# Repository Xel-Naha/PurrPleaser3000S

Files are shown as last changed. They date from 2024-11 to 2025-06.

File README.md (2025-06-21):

<p align="center">
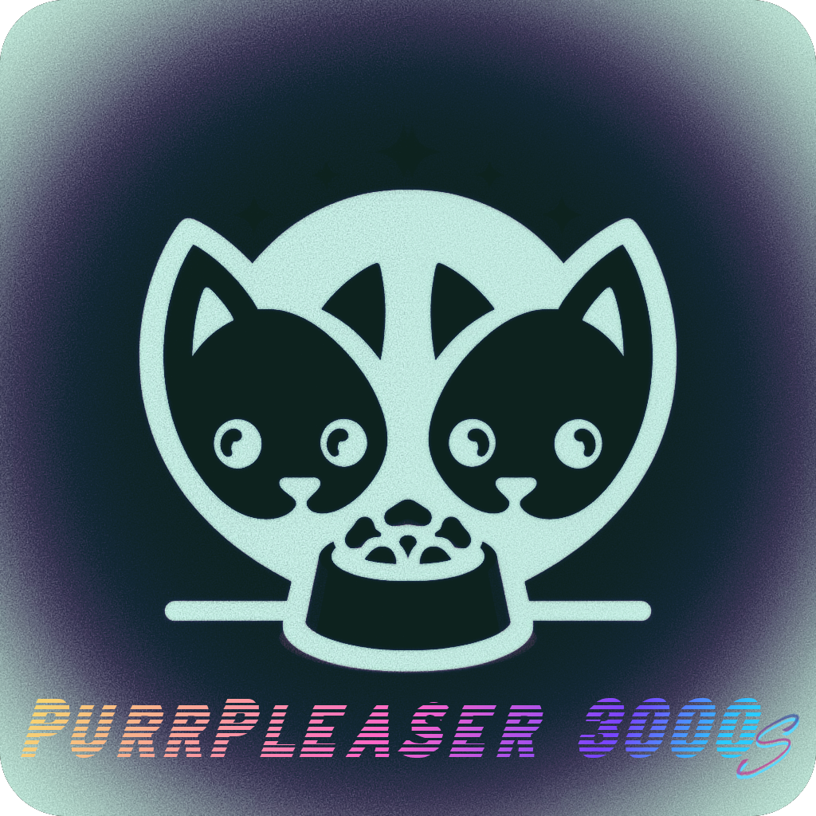
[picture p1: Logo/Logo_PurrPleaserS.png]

</p>

# PurrPleaser3000 Single

This is the PurrPleaser 3000S, an automatic cat feeder for a single cat. With this cat feeder you’ve got a complete project to build your own feeder which automatically dispenses food for your cat over weeks. Further it is fully configurable via Home Assistant, to for example change feeding times, feeding amounts, give treats etc. Further, this project contains everything you needs, if you have basic electronics + Arduino knowledge and a 3D-printer at hand. This is actually the fifths iteration of my cat feeder build, but the first one I publish – so it has been tested and improved over the years. 
Further details and guidance can be found at: climbing-engineer

## Multiple Cats

This project has originally started as a dual feeder for two cat; unfortunately one of my cats has passed – so it is a single feeder now. Nevertheless, the code is flexible and actually still optimized for multiple cats and can be adapted accordingly. Also the repo with an example for two cats still exist, although it is not updated anymore: https://github.com/Poing3000/PurrPleaser3000

## Usage

  1. Build your cat feeder. You can use the 3D Files here (also on: [Printables](https://www.printables.com/model/1144196-purrpleaser3000s-an-automatic-single-cat-feeder)) and the schematics to build your driver board our use the provided design to let it manufacture. Further info at: climbing-engineer
  2. Download all external dependencies via the Arduino library manager.
  3. Download this repository  / folder [FP3000_PicoW](https://github.com/Poing3000/PurrPleaser3000S/tree/main/PP3000S_PicoW).
  4. Open FP3000_PicoW.ino  in the FP3000_PicoW folder.
  5. Change the settings in Credentials.h and PP3000S_Config.h according to your needs.
  6. IMPORTANT,  allow Flash to be used for LittleFS (Go to Tools -> Flash Size -> FS: 64kb)!
  7. Flash your Raspberry Pico W.
  8. Run it / let it be detected buy your home assistant (will be integrated automatically).
  9. Configure your home assistant, e.g. build a Dashboard like in the examples: [HomeAssistant](https://github.com/Poing3000/PurrPleaser3000S/tree/main/HomeAssistant).
  10. Configure your Feeder via Home Assistant (Calibrate the scale, set your schedule..).
  11. Enjoy – See Home Assistant / Interface below.

## Software

> [!NOTE]
> This code (C++) is written to run on a Raspberry Pico W.

> [!NOTE]
> At the moment the feeder uses Home Assistant as an interface. It is easily possible to extent the code to implement a website or so; however, I don’t need it at the moment – feel free to implement changes that suit your needs.
### Pico 2 W (RP2350) boards
Pico 2 W requires the latest Pico SDK with `hardware/powman.h` and the `PICO_RP2350` define so the powman timer works.

### External Dependencies (Libraries)
You will need to download and install the following external Arduino libraries:

| Name | Link | Version Tested |
| --- | --- | --- |
| TimeZone.h 	  | https://github.com/JChristensen/Timezone  | 1.2.4 |
| ArduinoHA.h  | https://github.com/dawidchyrzynski/arduino-home-assistant  | 2.1.0 |
| Arduino_DebugUtils.h | https://github.com/arduino-libraries/Arduino_DebugUtils | 1.4.0 |
| MCP23017.h | https://github.com/wollewald/MCP23017_WE/tree/master | 1.6.8 |
| TMCStepper.h | https://github.com/teemuatlut/TMCStepper | 0.7.3 |
| HX711.h | https://github.com/RobTillaart/HX711 | 0.5.2 |

### How this code works

First of all, I am not a professional, nor am I really good at coding; however, it works and I tried my best in my free time. In case you’ve got improvements / suggestions, please feel free to implement them.

> [!NOTE]
> At first you should note that this code has been specifically written for the Raspberry Pico W. It further uses both cores of the RP2040, whereat at communication, WiFi, scheduling etc. runs on Core 0 and all hardware (sensors, drivers, motors) linked functionalities run on Core 1.

The main parts you should be interested in when reading this are:

+ **PP3000S_PicoW.ino** 
    
    This is the main Arduino sketch, which should give you an idea how the feeder basically works and what dependencies it uses. However, in case you don’t want to change any functionality this should stay as it is.

+ **PP3000S_Config.h**

    This is the configuration file, which allows to change fundamental settings to your needs. Some things are that you certainly want to change, e.g. your cat name. But there are also further settings mostly tailored to the given design, so if you don’t want to change it, most settings can be left as is (e.g. connections to the pico board pins, motor driver settings etc.).

+ **Credentials.h**

    This is your secrets file, it lets you change your wifi settings etc. and helps you keep them secret for example in case you are uploading your code on your on github etc. (https://arduino.stackexchange.com/questions/40411/hiding-wlan-password-when-pushing-to-github).

In case you need more details or want to change things, you should have a look a the external libraries (see above) and the libraries I have created (see below).

### Internal Dependencies
The code has some generic (working with more than one cat) helper functionalities in FoodSchedule.h/.cpp and SupprtFunctions.h. These mostly extent the main .ino file and help to de-clutter the code. Then there are FP3000.h/.cpp and SpeedyStepper4Purr.h/.cpp, both belong to the heart piece of the cat feeder, the [FoodPump3000](https://github.com/Poing3000/FoodPump3000).  The food pump considers the actual working hardware of the cat feeder and can also be used on it’s own / implemented in another project. All necessary info can be found at the FoodPump3000 repository and at climbing-engineer.

## Home Assistant / Interface
Currently the feeder is designed to be used along with Home Assistant ([ArduinoHA](https://github.com/dawidchyrzynski/arduino-home-assistant)). Though, if you need another interface it should be easy to extent the code, e.g. to use an external display or to provide a webserver.

When your MQTT settings are correct in Credentials.h, the cat feeder should automatically appear in your device list without any notification (Settings > Devices & Services > MQTT > Devices > "Your Feeder Name"). This provides you the basic controls over the feeder:

1. Set individual feeding amounts (max. 4x feedings /day).
2. Autotune – This autotunes the stall detection with the TMC2209 driver for error detection (I found it not to be too important, though I've spend a lot of time on it). If you've got food in the feeder, prepare to collect a lot of dispensed food!

> [!Important]
> In any case, do autotuning once – it helps with error detection and handling!

4. Calibrate – This calibrates the scale and needs to be done the first time the scale is beeing used.
> [!Tip]
> When you press "Calibrate", you'll receive messeages, telling you what you need to do: "You've got **20 seconds to empty the scale bucket** > then the scale tares > then you've go **20 seconds to put 20g into the bucket** > the scale is calibrated.

6. Set a daily feeding amount. This overrides / sets the individual amounts and spreads the daily amount over four feedings.
7. Feeding Times (Hour + Minute). This allows to set the (max.) four feedings times at which the set amount of food will be dispensed.
8. Reset. Restarts the feeder (calibrations are saved permenently).
9. Save Schedule. Feeding amounts and time are only permenently saved if you press this button.
10. Stall Warnings – I don't really use it. It gives you a warning whenever a stall has been detected from the stepper drivers (may be sensitive).
11. Treat. Treat your cat!
12. Amount to be dispensed for a treat. Could also be used for extra manual feeding (e.g. by a Home Assistant routine).

Further, there are a few sensors that provide you dome informatiob over the feeder.
1. Days until empty. This is a rough estimate of how many days of food are left in the feeder.
> [!Tip]
> Days until empty only works if you've got the top and bottom fill sensor installed. Further you need to set the capacity yourself in PP3000S_CONFIG.h. Measure the amount: 1. when the bottom sensor is just covered (LOW_CAP) and from there 2. when the top sensor is just covered (LOW_CAP).

3. Debug tells you if there is something wrong (sensor failure, scale failure etc.).
4. Last amount that has been fed.
5. Status tells you what the feeder is currently doing (Standby, Feeding..).

> [!Note]
> In case something goes wrong the feeder will give everything to feed your cat. In case an error has been detected – e.g. scale not working -  the feeder will go into an emergency mode (no scale, increased current...) and will try to roughly dispense food at feeding times. Depending on the error type, the feeder may also be able to solve the issue on its own (freeing a stuck slider etc.).

I've created myself a dashboard that uses [Mushroom cards](https://github.com/piitaya/lovelace-mushroom). You find an example in the [Home Assistant folder](HomeAssistant).

## Hardware
### 3D Print
You will need a case, the food pump, a food silo and a scale. If you want to use my design feel free to 3D print it. If you want, you can change my design – all SolidWorks files are located in the ([Hardware/CAD](https://github.com/Poing3000/PurrPleaser3000S/tree/main/CAD)) folder.

In case you use my design, it should be straight forward. In regard to printing, I did not use any significant settings. Most parts do not need much infill, rather do an extra loop on the walls. Tolerances may depend on your printer – tough I designed the gears to be hard to attach to the motors (once they are on, I can’t get them of without breaking. For the bigger (case) parts, I’ve used a 0.6 nozzle, though this was only to speed things up. Further I had issues with warping for the big parts (even with PLA), but it still fits / looks alright.

Materials I’ve used:
Case:	PLA
Silo:	PLA
Rest:	PETG / ABS
Optional
Seals:	TPU

### Parts to buy
**Case:**
- Filament
- Threaded inserts (I’ve used a standard set from Ruthex (M2-M5) – the short version is fine, though most holes are designed for the longer/standard ones; the outer case is better of with the short ones (M4)).
- Screws (just get yourself a set of M-Screw on Amazon etc. – they are cheap.)

**Electronics:**
*Outside*
1x 12V Power Supply (in case you want it fail safe you could e.g. use an Eaton 3S Mini UPS)

*In case*
- 2x TCRT 5000 optical sensor (silo fill sensors)
- 2x TCST2202 optical sensor (end-stop sensors)
- 2x NEMA-17 Stepper Motors (e.g.17HS08-1004S)
- 1x HX711 weighing wensor module
- 1x 500g Mini Load Cell (e.g. 500g TAL221 / SEN-14728)

*On PCB*
- 1x Raspberry Pico W
- 2x TMC2209 Stepper Driver (e.g. S2209 V4.0 form Fysetc)
-  Resistors:
 2x 10 kΩ
 1x 1 kΩ
 2x 100 Ω
- 2x 100 uF Capacitor
- 6x 4-Pin JST / XH Connectors (male + female)
- Standard Pin Headers (for raspberry, connections… get a few, they are always good to have)
- 1x Screw Terminal (e.g. DORABO DB128V-5.0-2P-OG-S)
*Optional:*
- 5x 4-Pin JST / XH Connectors (male + female) – extra GPIO (e.g. for a display)
- 9x 100 nF Capacitor  - no really needed but could be beneficial
- 6x Standard Jumpers - to easily apply board settings
- 1x Screw Terminal (e.g. DB128V-5.0-2P-GY-S) – in case you want to provide external 3.3V or source it from the board.
- 1x 3.3V Power Supply (from 12V input) – I use a separate 3.3V power supply from the one that it is on the pico, just to be on the safe side (pico: 300mA max) and to be able to add further things like a display etc. You can use e.g. a LMxx / TSR 1-2433 / D36V28F3 on board or supply the board from an external 3.3V supply. >> Don’t forget to short JEN1 if you don’t use the internal 3.3V Pico power supply. <<

Generally all CAD files and schematics should be self explaining (further info on climbing-engineer). You do not need to use my PCB design / buy a PCB, but I suggest to orientate on my schematics. Further my schematics already include some future improvements possibilities (access to GPIOs) and provide some flexibility in regard to the power supply. 
	
## Possible Future Improvements
- [ ] Calibrate Scale With Food - Calibrate the scale by dispensing food, manually measuring the dispensed amount, and providing feedback of the measured amount back to the feeder for calibration.
- [ ] Over the Air Updates (OTA)
- [ ] Support Display
- [ ] Web Interface

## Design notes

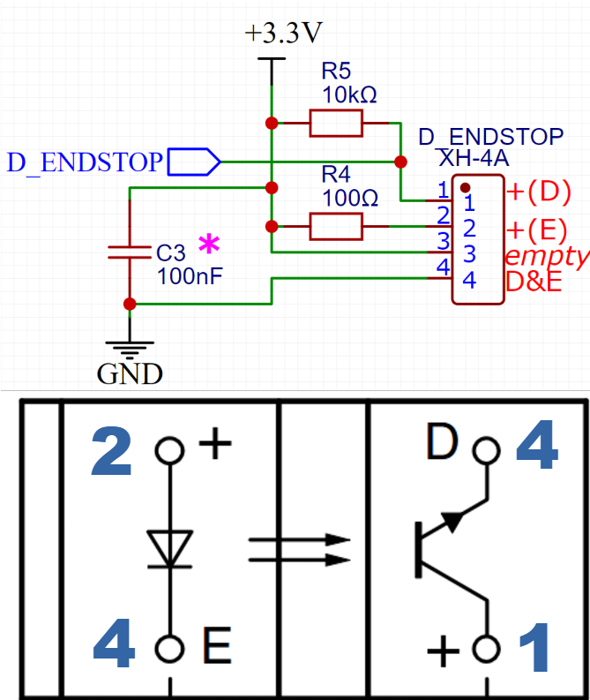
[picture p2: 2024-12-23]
PCB/TCST2202_PIN_Connection.png

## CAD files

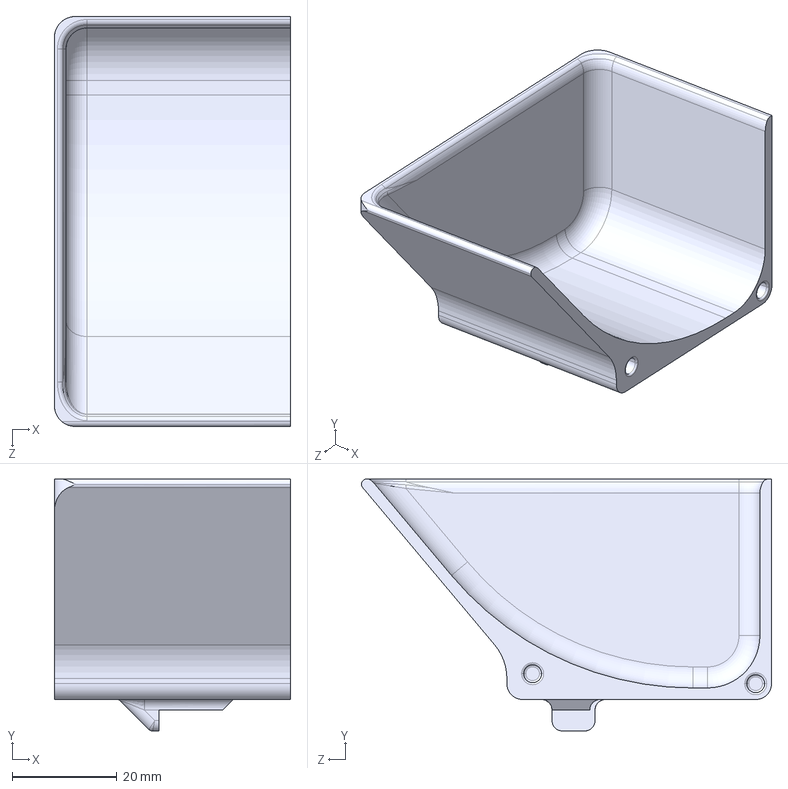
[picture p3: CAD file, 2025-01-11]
CAD/Print/Scale/CF5V_Scale_Dumper_Main.STEP
45.0 x 48.0 x 78.1 mm

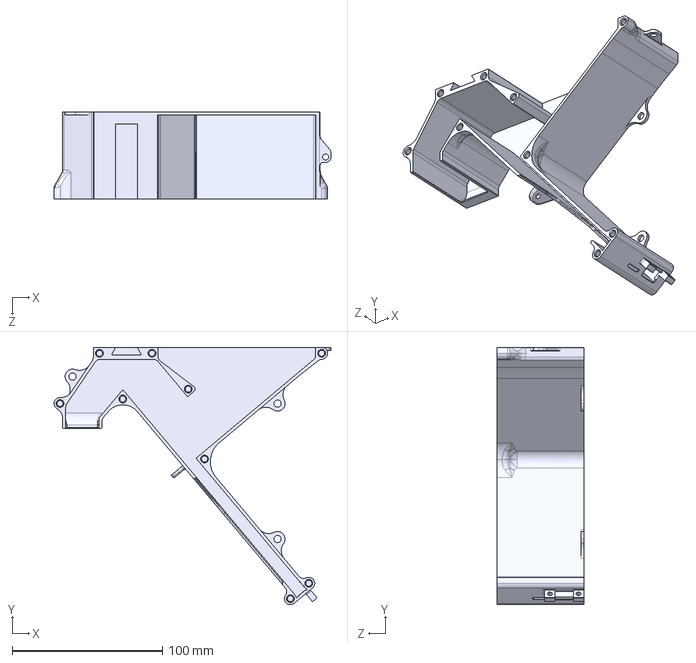
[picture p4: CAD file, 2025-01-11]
CAD/Print/Pump/CFV5_Pump_MainBody.STEP
184.5 x 171.4 x 58.0 mm

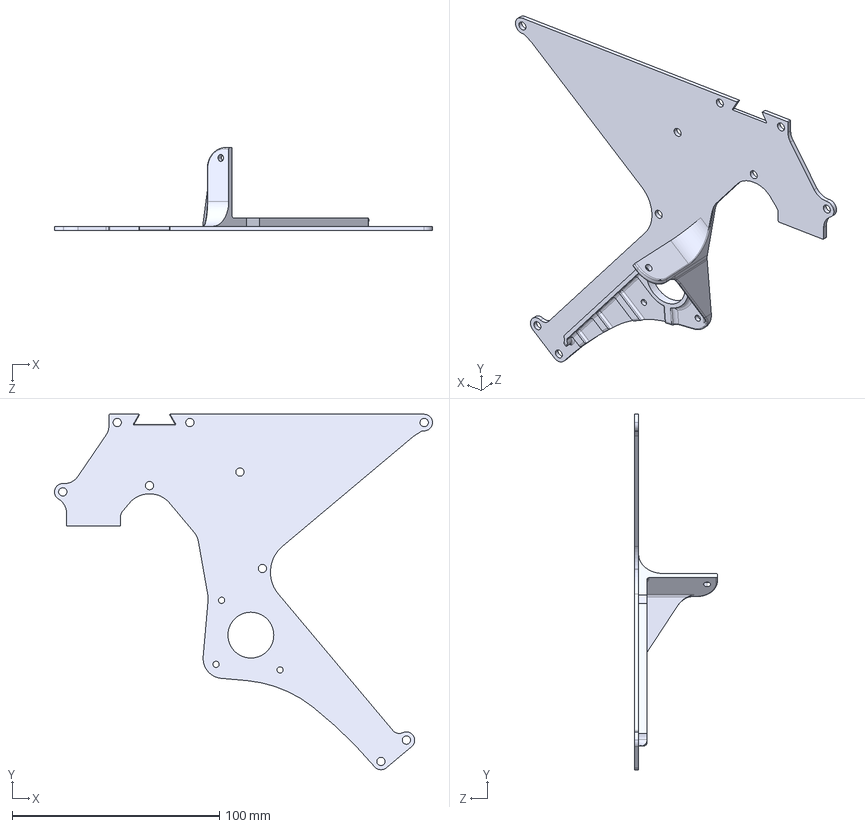
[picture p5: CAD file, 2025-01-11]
CAD/Print/Pump/CFV5_Pump_MainBody-Front.STEP
182.3 x 171.4 x 40.0 mm

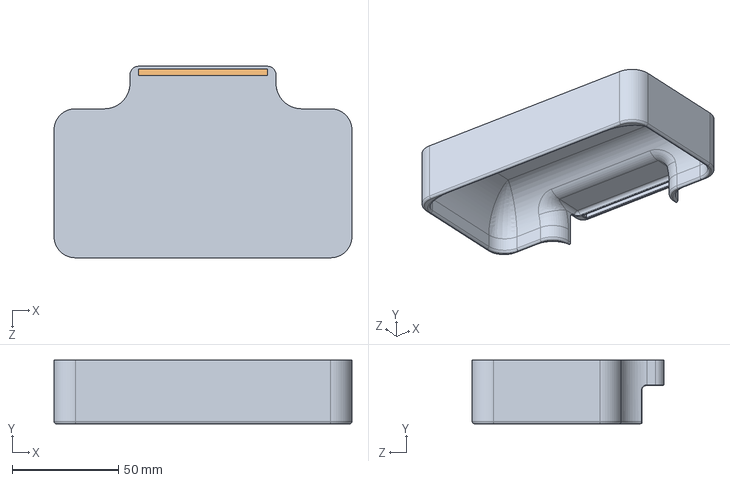
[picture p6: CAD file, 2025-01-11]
CAD/Print/Case/CFV5_SCase_Bowl.STEP
140.0 x 30.0 x 90.0 mm

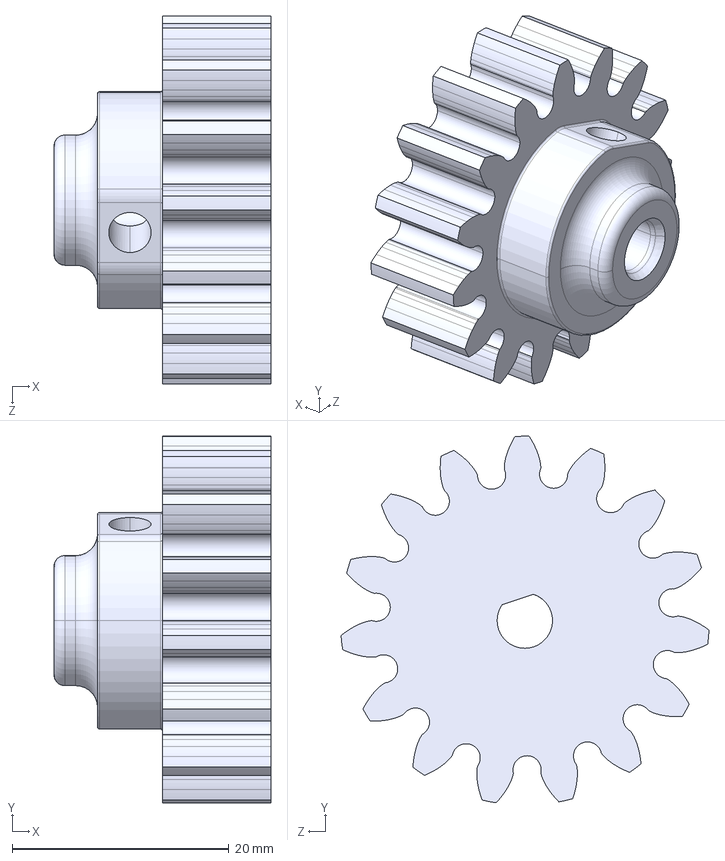
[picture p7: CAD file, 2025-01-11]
CAD/Print/Pump/CFV5_Pump_Gear.STEP
20.0 x 33.8 x 33.9 mm

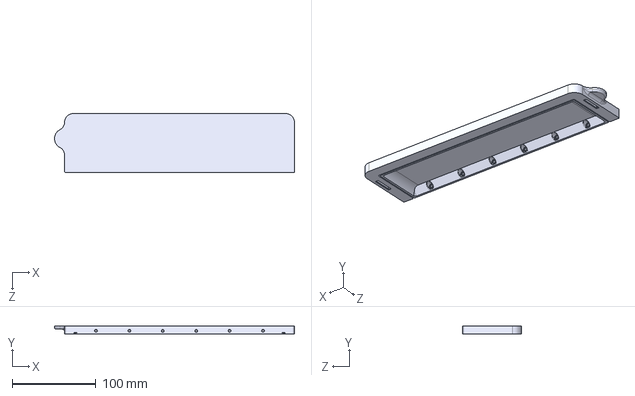
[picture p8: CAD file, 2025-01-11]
CAD/Print/Case/CFV5_SCase_Lid-Split-Front.STEP
287.2 x 10.0 x 70.6 mm

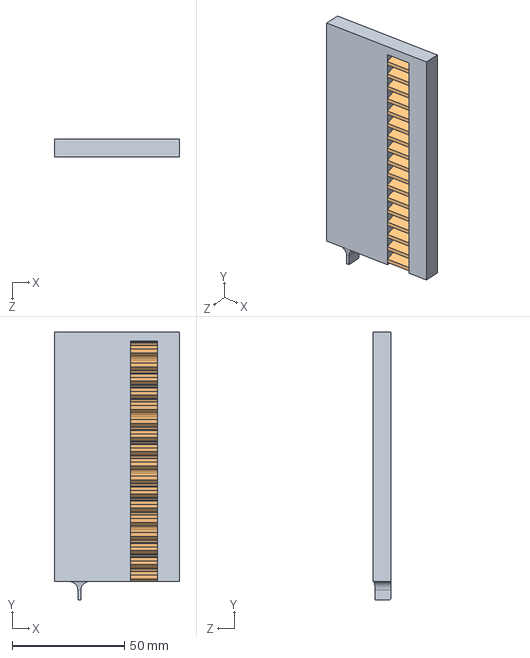
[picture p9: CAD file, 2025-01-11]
CAD/Print/Pump/CF5V_Pump_Slider.STEP
55.8 x 119.2 x 7.80 mm
CFV5_Slider
CFV5_Slider_LinearGear

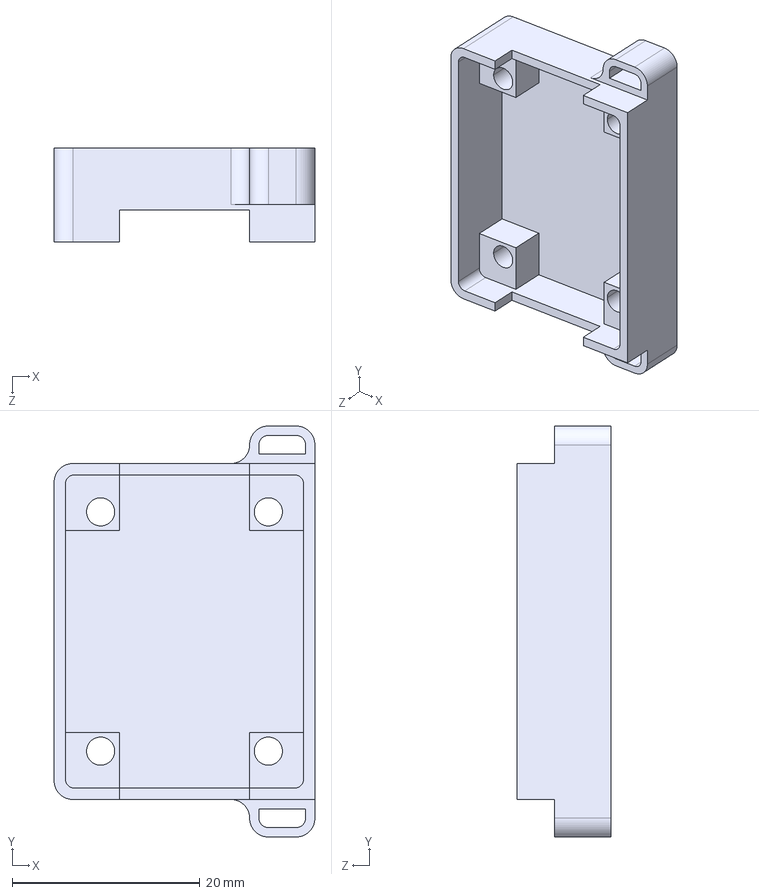
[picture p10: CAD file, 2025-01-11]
CAD/Print/Scale/CFV5_Scale_HX711_Cover.STEP
27.8 x 43.8 x 10.0 mm

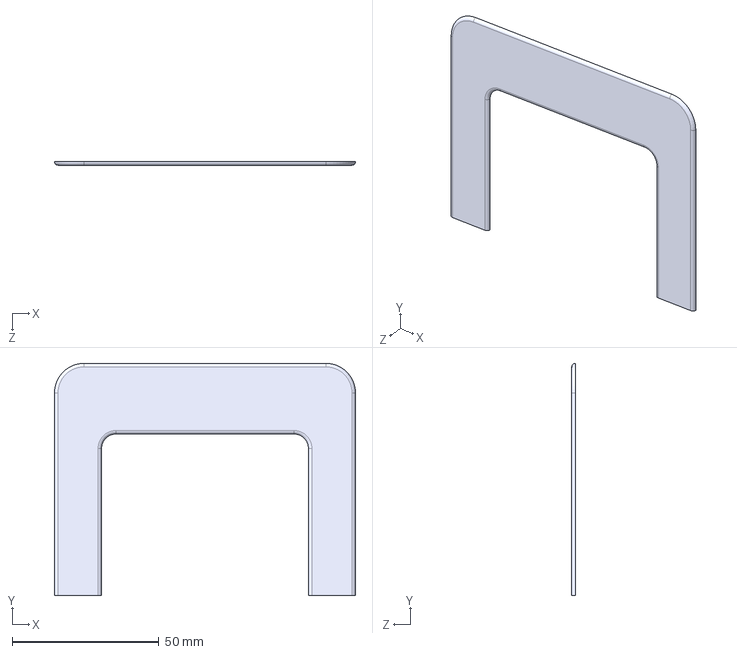
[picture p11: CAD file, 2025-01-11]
CAD/Print/Case/CFV5_SCase_Front_Decor.STEP
102.4 x 79.0 x 1.20 mm

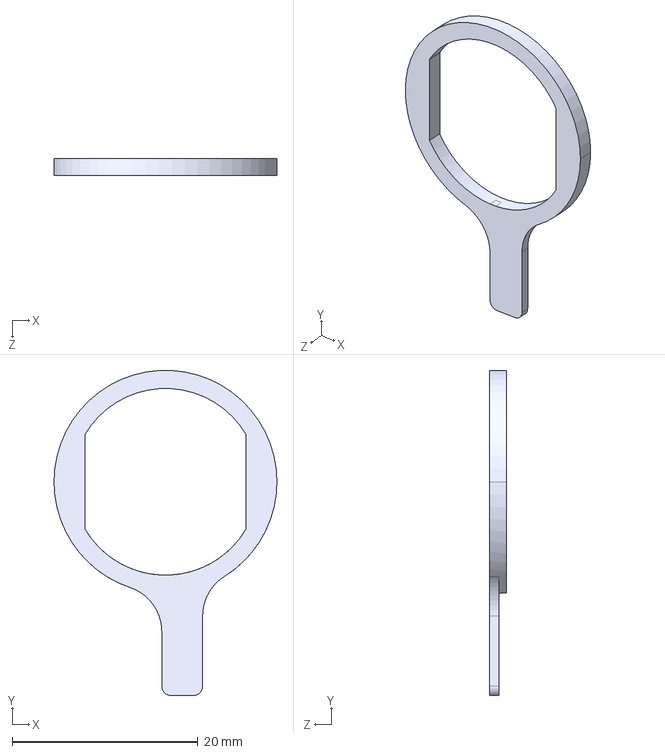
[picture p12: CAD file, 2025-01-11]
CAD/Print/Scale/CFV5_Scale_SensorTarget.STEP
24.0 x 35.0 x 1.80 mm

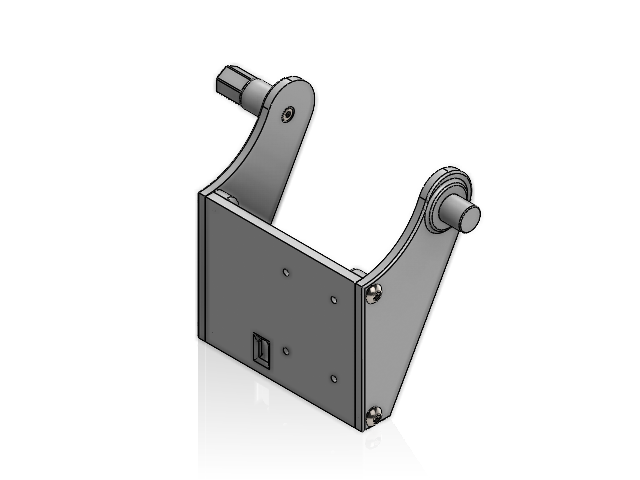
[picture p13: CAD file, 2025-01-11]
CAD/Solid/CFV5_Dumper_Manipulator.SLDASM
CFV5_Dumper_Manipulator_LHW
ISO 4762 M2 x 16 - 16N
CFV5_Dumper_Manipulator_BW
ruthex RX-M3-5,7.stp x 4
CFV5_Dumper_Manipulator_RHW
ISO 7380 - M3 x 8 - 8S x 4

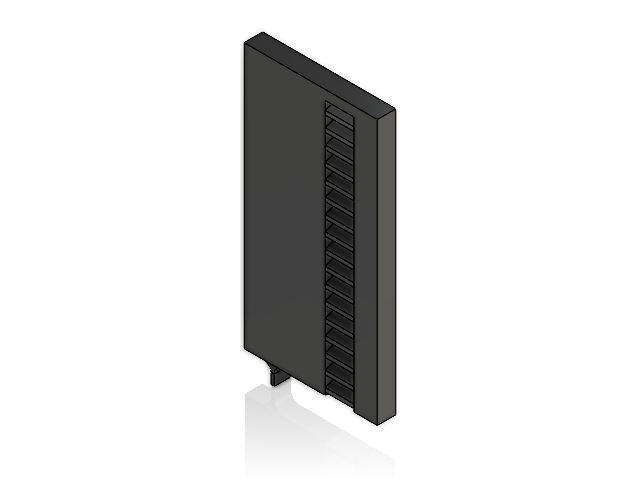
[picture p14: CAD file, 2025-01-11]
CAD/Solid/CF5V_Pump_Slider.SLDASM
CFV5_Slider
CFV5_Slider_LinearGear

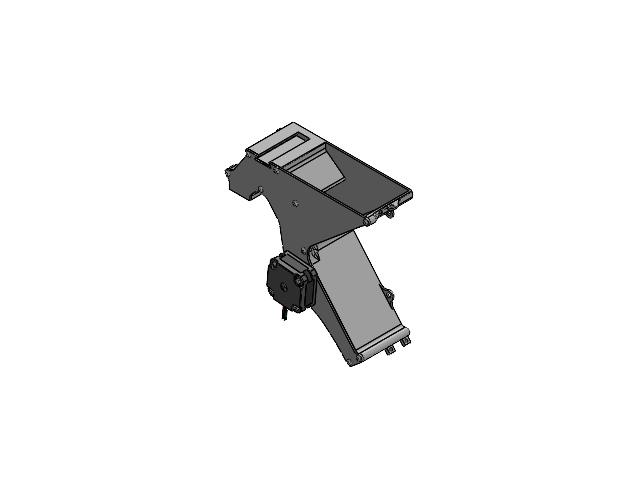
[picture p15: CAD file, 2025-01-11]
CAD/Solid/CF5V_Pump.SLDASM
CFV5_Pump_MainBody
CFV5_Pump_MainBody-Front
17HS08-1004S
CFV5_Pump_Gear
CFV5_Slider
CFV5_Slider_LinearGear
ruthex RX-M3-5,7.stp x 10
ISO 7380 - M3 x 6 - 6N x 9
ISO 7380 - M3 x 6 - 6S x 3
ISO 7380 - M3 x 8 - 8N
ISO - 4035 - M3 - N
DIN 916 - M3 x 6-N

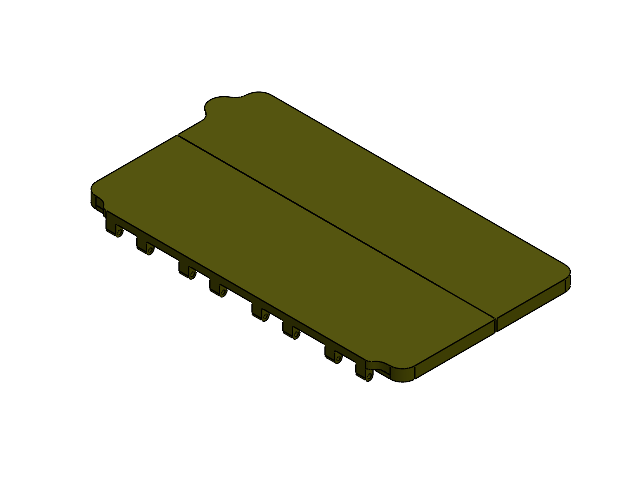
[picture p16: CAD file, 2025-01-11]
CAD/Solid/CF5Vs_Lid.SLDASM
CFV5_SCase_Lid-Split-Back
CFV5_SCase_Lid-Split-Front
ISO 4762 M3 x 8 - 8N x 6
ISO - 4035 - M3 - N x 6
CFV5_SCase_Lid_Seal

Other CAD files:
CAD/Solid/ruthex_RX-M4x8.1.SLDASM
CAD/Solid/ruthex_RX-M2x4.SLDASM
CAD/Solid/CF5V_Scale_Dumper_Main.SLDPRT
CAD/Solid/CFV5_Pump_MainBody.SLDPRT
CAD/Print/Case/CF5Vs_PCB_Plate.STEP
CAD/Print/Case/CF5Vs_SCase_Front_Low.STEP
CAD/Print/Case/CF5Vs_SCase_Front_Top.STEP
CAD/Print/Case/CF5Vs_SCase_Mid_Low.STEP
CAD/Print/Case/CF5Vs_SCase_Mid_Top.STEP
CAD/Print/Case/CF5Vs_SCase_Plate.STEP
CAD/Print/Case/CFV5_SCase_Lid-Split-Back.STEP
CAD/Print/Case/CFV5_SCase_Lid_Seal.STEP
CAD/Print/Case/CFV5_SCase_Silo.STEP
CAD/Print/Case/CFV5_SCase_Silo_Seal.STEP
CAD/Print/Scale/CF5V_Scale_Dumper_Side.STEP
CAD/Print/Scale/CFV5_Dumper_Manipulator_BW.STEP
CAD/Print/Scale/CFV5_Dumper_Manipulator_LHW.STEP
CAD/Print/Scale/CFV5_Dumper_Manipulator_RHW.STEP
CAD/Print/Scale/CFV5_Scale_Baseplate.STEP
CAD/Print/Scale/CFV5_Scale_Bottom.STEP
CAD/Print/Scale/CFV5_Scale_Frame_LH.STEP
CAD/Print/Scale/CFV5_Scale_Frame_RH.STEP
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

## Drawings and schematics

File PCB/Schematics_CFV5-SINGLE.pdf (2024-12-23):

0b00

0b10

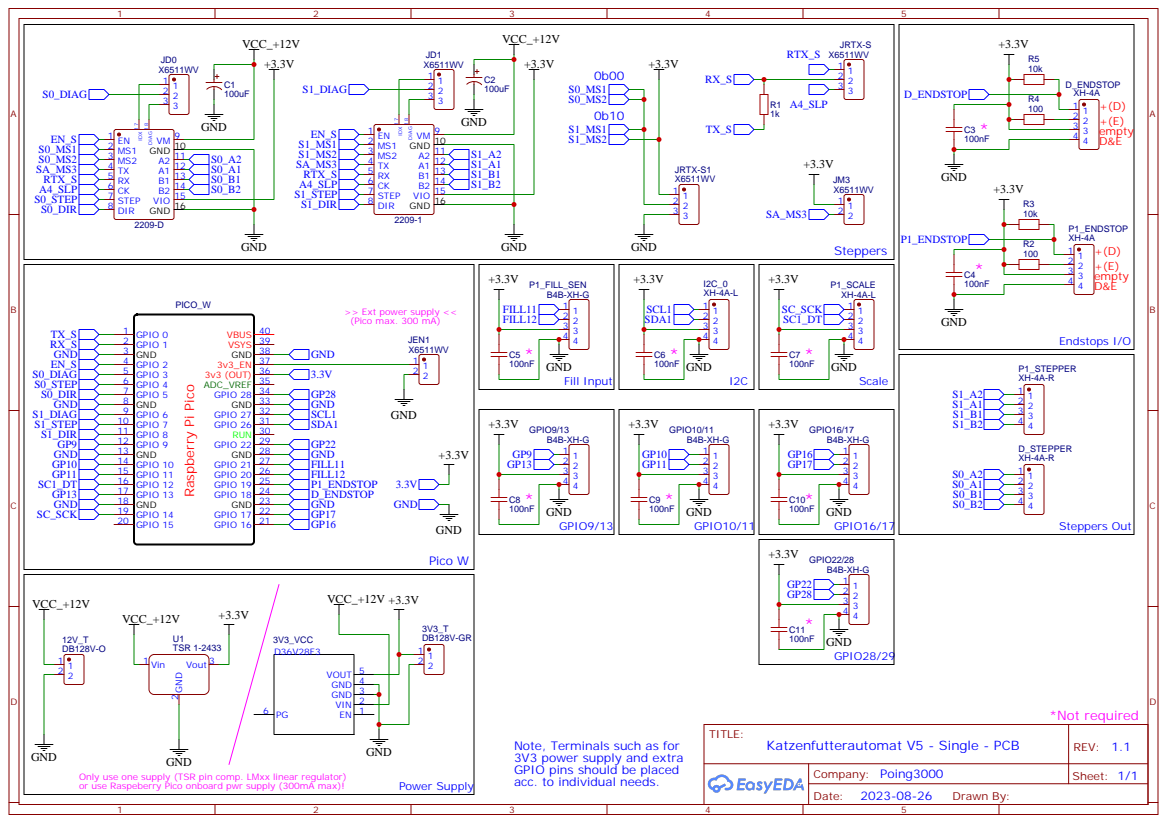
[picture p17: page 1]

Note, Terminals such as for
3V3 power supply and extra
GPIO pins should be placed
acc. to individual needs.

Only use one supply (TSR pin comp. LMxx linear regulator)
or use Raspeberry Pico onboard pwr supply (300mA max)!

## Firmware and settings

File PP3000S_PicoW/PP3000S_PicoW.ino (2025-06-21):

/*
 * Name:	PurrPLeaser3000S
 * Author:	Poing3000
 * Status:	Beta
 *
 * Description:
 * This code is for the PurrPleaser3000S.
 * It is built for a Raspberry Pico W and a TMC2209 stepper driver.
 * Further info at: https://github.com/Poing3000/PurrPleaser3000S
 *
 * NOTE: Allow Flash to be used for LittleFS in the Arduino IDE settings (Tools -> Flash Size -> FS: 64kb)!
 * 
 * EXTERNAL DEPENDENCIES:
 * ---------------------------------------------------------------------------------------------------
 * Please install the following libraries via the Arduino Library Manager:
 *  NAME                    LINK                                                        VERSION TESTED
 *  TimeZone.h            - https://github.com/JChristensen/Timezone                    1.2.4
 *  ArduinoHA.h           - https://github.com/dawidchyrzynski/arduino-home-assistant   2.1.0
 *  Arduino_DebugUtils.h  - https://github.com/arduino-libraries/Arduino_DebugUtils     1.4.0
 *  MCP23017.h            - https://github.com/wollewald/MCP23017_WE/tree/master        1.6.8
 *  TMCStepper.h          - https://github.com/teemuatlut/TMCStepper                    0.7.3
 *  HX711.h               - https://github.com/RobTillaart/HX711                        0.5.2
 * ---------------------------------------------------------------------------------------------------
 * 
 */

 // CONFIGURATION:
 // ----------------------------------------------------------
 // Please find all configuration in the PP3000_CONFIG.h file.
 // The following code should not need any changes.
 // Any settings should be done in the configuration file.
 // ---------------------------------------------------------*

 // LIBRARIES:
 // ----------------------------------------------------------
 // External
#include <Wire.h>
#include <WiFi.h>
#include <Timezone.h>
#include <ArduinoHA.h>
#include <Arduino_DebugUtils.h>

// Pico SDK specific
#include "src/time_compat.h"

// Local
#include "Credentials.h"
#include "PP3000S_CONFIG.h"
#include "src/FoodSchedule.h"
#include "src/FP3000.h"
// ---------------------------------------------------------*

// CREATE DEVICES:
// --------------------------------------------------------------------------------------------
// Port Expander
MCP23017 mcp = MCP23017(MCP_ADDRESS);		// (Don't delete, aut. ignored if EXPANDER = false)

// Dumper Drive
FP3000 DumperDrive(MOTOR_0, STD_FEED_DIST, PUMP_MAX_RANGE, DIR_TO_HOME_0, SPEED, STALL_VALUE,
	AUTO_STALL_RED, SERIAL_PORT_1, R_SENSE, DRIVER_ADDRESS_0, mcp, EXPANDER, MCP_INTA);

// Pump
FP3000 Pump_1(MOTOR_1, STD_FEED_DIST, PUMP_MAX_RANGE, DIR_TO_HOME_1, SPEED, STALL_VALUE,
	AUTO_STALL_RED, SERIAL_PORT_1, R_SENSE, DRIVER_ADDRESS_1, mcp, EXPANDER, MCP_INTA);
// -------------------------------------------------------------------------------------------*

// SET TIMEZONE:
// --------------------------------------------------------------------------------------------
TimeChangeRule DLT = { "CEST", WEEK_S, DOW_S, MON_S, HOUR_S, UTC_S };
TimeChangeRule SDT = { "CET",  WEEK_W, DOW_W, MON_W, HOUR_W, UTC_W };

// Create PicoRTC (to be used for scheduling)
FS3000 PicoRTC(DLT, SDT, NTP_SERVER);
// -------------------------------------------------------------------------------------------*

// PURR PLEASER SPECIFICS
// --------------------------------------------------------------------------------------------
// Special Variables
// ============================================================================================
// FoodPump Modes
enum FPMode : byte {
	IDLE,
	FEED,
	CALIBRATE,
	AUTOTUNE,
	EMGY
};
// The Core 1 loop switches between different operating modes.
// The mode is set by Core 0. Default is IDLE.
byte Mode_c1 = IDLE;

// Treat Amounts (can also be used to trigger manual feeding with a specific amount)
float treatAmount1 = TREAT_AMT;

// ===========================================================================================*

// Special Functions
// ============================================================================================
// NOTE: The following are not libraries - they are just header files incl. additional code /
// functions used in this main file. Again, they are not libraries. Hence, moving these
// "#includes" may cause errors! (This way was chosen in order to declutter this main file.)
#include "src/Communication.h"
#include "src/SupportFunctions.h"

// -------------------------------------------------------------------------------------------*

// PHYLOSOHPY:
// --------------------------------------------------------------------------------------------
// This code uses the two cores of the Raspberry Pico W.
// Core 0 is used for communication, scheduling, and handling the WiFi and MQTT connections.
// Core 1 is used for driving hardware and reading the sensors.
// --------------------------------------------------------------------------------------------*

// SETUP - CORE 0:
// --------------------------------------------------------------------------------------------
void setup() {

	// Debugging
	Debug.setDebugLevel(DEBUG_LEVEL);
	if (Debug.getDebugLevel() >= 0) {	// Give time to open serial monitor
		delay(500);
	}

	// Connect to the WiFi network
	DEBUG_DEBUG("Connecting to %s", WIFI_SSID);
	WiFi.begin(WIFI_SSID, WIFI_PASSWD);

	// Setup PicoRTC (feeding scheduling)
	DEBUG_DEBUG("Setting up PicoRTC");
	PicoRTC.SetupFeedClock();

	// Setup Communication
	DEBUG_DEBUG("Setting up Communication");
	setupCommunication_c0();			// (Communication)

	// Setup Core 0 finished, allow Core 1 to start
	DEBUG_DEBUG("Core 0 setup finished, next Core 1.");
	rp2040.fifo.push(1); // 1 = OK
}
// -------------------------------------------------------------------------------------------*

// SETUP - CORE 1:
// --------------------------------------------------------------------------------------------
void setup1() {

	// Give Core 0 a head start, just in case.
	delay(100);

	// Setup Codes
	enum SetupCodes : byte {
		NOT_STARTED,
		OK,
		ERROR,
		WARNING
	};

	// Wait for Core 0 to finish setup
	while (rp2040.fifo.pop() != OK);

	// Pin Setup
	pinMode(DRIVER_ENABLE, OUTPUT);
	pinMode(LED_BUILTIN, OUTPUT);
	pinMode(DIAG_1, INPUT);
	digitalWrite(DRIVER_ENABLE, HIGH);				// Disable Driver
	digitalWrite(LED_BUILTIN, LOW);					// Visual indication that PurrPleaser is not started.

	// Driver Setup
	SERIAL_PORT_1.begin(115200);

	// Setup Pump
	byte setupResult = NOT_STARTED;					// Return from setup functions
	digitalWrite(DRIVER_ENABLE, LOW);				// Enable Driver

	// Setup Motor 0
	setupResult = DumperDrive.SetupMotor(CURRENT, MIRCO_STEPS, TCOOLS, STEP_0, DIR_0, LIMIT_0, DIAG_0, ACCEL);
	if (setupResult != OK) {
		ReceiveWarningsErrors_c1(DumperDrive, MOTOR_0);			// (Support Function)
	}

	// Setup Motor 1
	setupResult = Pump_1.SetupMotor(CURRENT, MIRCO_STEPS, TCOOLS, STEP_1, DIR_1, LIMIT_1, DIAG_1, ACCEL);
	if (setupResult != OK) {
		ReceiveWarningsErrors_c1(Pump_1, MOTOR_1);				// (Support Function)
	}

	// Setup Scale 1
	setupResult = Pump_1.SetupScale(SCALE_NVM_1, DATA_PIN_1, CLOCK_PIN_1);
	if (setupResult != OK) {
		ReceiveWarningsErrors_c1(Pump_1, SCALE_1);				// (Support Function)
	}

	// Setup finished
	digitalWrite(LED_BUILTIN, HIGH);							// Visual indication that PurrPleaser has started.

}
// END OF SETUP++++++++++++++++++++++++++++++++++++++++++++++++++++++++++++++++++++++++++++++++
//+++++++++++++++++++++++++++++++++++++++++++++++++++++++++++++++++++++++++++++++++++++++++++++


// MAIN PROGRAM (LOOP):
	// CORE 0
void loop() {

	// ===============================================================
	// This is the main loop for Core 0. It is used to handle the
	// communication between Core 0 and Core 1, as well as to check
	// the feeding schedule and send feeding commands to Core 1.
	// Further, it is used to handle the WiFi and MQTT connections.
	// ===============================================================

	// EXAMPLE CODE:
	// There is an example serial user interface at the far bottom of this file,
	// uncomment (also code at the bottom) for testing etc:
	//exampleSerialInterface();

	// Check for data from Core 1
	PopAndDebug_c0();			// (Support Function)

	// Check if it is time to feed, if send feeding command to Core 1
	CheckTimeAndFeed_c0();		// (Support Function)

	// Check WiFi
	checkWifi();				// (Support Function)

	// Handle MQTT
	mqtt.loop();

	// -------------------------------------------------------------------------------------------------
}

// CORE 1
void loop1() {

	// ===============================================================
	// This is the main loop for Core 1. It is used to handle the
	// hardware and sensors, as well as to drive the feeding process,
	// as commanded by Core 0.
	// ===============================================================

	// Variables
	// --------------------------------------------------------------------------------------------------------

	// Syntax for function returns
	enum ReturnCode : byte {
		BUSY,
		OK,
		ERROR,
		WARNING
	};

	// Feeding Modes
	enum FeedingMode : byte {
		PRIME,
		APPROX,
		ACCURATE,
		EMPTY
	};
	static byte feedMode = PRIME;

	// Variables for Priming
	static byte dumperReturn = BUSY;
	static byte pump1Return = BUSY;

	// Calibration Status (check numbers in CALIBRATE below)
	byte calStatus = 0;
	byte prevCalStatus = 1;

	// Feeding Amount in g (default 10g)
	static float feedingAmount_1 = 10.0;

	// Amount fed last time (default 0g)
	static float lastFed_1 = 0.0;

	// Feeding Amount correction in g (default 0g)
	static float feedingCorrection_1 = 0.0;

	// Feeding Cycles (checks for empty scale)
	static byte feedCycles = 0;

	// Time keeping for intervals
	static unsigned long lastTime = 0;
	const unsigned long checkInterval = 10000; // 10 seconds
	unsigned long currentTime = millis();

	// -------------------------------------------------------------------------------------------------------*

	// Operation Mode Settings
	// --------------------------------------------------------------------------------------------------------

	// Set Mode (and if available feeding amount) - from Core 0
	PopData_c1(Mode_c1, feedingAmount_1);					// (Support Function)

	// Check if Mode_c1 is in its allowed range and send to Core 0 if changed.
	static byte oldMode_c1 = 99;							// force sending at start (e.g. after reset)
	if (Mode_c1 > EMGY) {
		// Unexpected Mode set, go to IDLE
		PackPushData('W', 99, 7);							// 99 - no device, 6 - invalid mode (Support Function)
		Mode_c1 = IDLE;
	}
	else if (Mode_c1 != oldMode_c1) {
		PackPushData('S', 99, Mode_c1);						// 99 - no device (Support Function)
		oldMode_c1 = Mode_c1;
	}
	// -------------------------------------------------------------------------------------------------------*


	// MAIN OPERATING MODES - CORE 1
	switch (Mode_c1) {
		// ----------------------------------------------------------------------------------------------------

	case IDLE:

		// ===============================================================
		// IDLE Mode is the default mode, where the device just waits for
		// commands from Core 0.
		// ===============================================================

		// Power Off unused devices
		Power_c1(false);							// Toggle e.g. Driver On/Off (Support Function)

		// Reset Feed Mode
		feedMode = PRIME;							// Reset feeding mode

		// Check every 10 seconds fill level
		if (currentTime - lastTime >= checkInterval) {
            lastTime = currentTime;
			checkFillLevel_c1(0);					// '0' because no feeding is done (Support Function)
        }


		break;
		// ----------------------------------------------------------------------------------------------------

	case FEED:

		// ===============================================================
		// This mode is to automatically dispense food until the desired
		// amount is reached. The amount is set by Core 0 and is measured
		// in grams by the selected scale. The feeding process works in
		// four steps:
		// 1. Prime: Go to start position (endstops) and tare the scale.
		// 2. Approx.: Move slider up and down to get an approximate
		//    amount of food, close to the desired amount (APP_OFFSET).
		// 3. Accurate: Move slider in a precise filling motion until
		//    the desired amount is reached.
		// 4. Empty: Do a final measurement and empty the scale dumper.
		// NOTE, the final scale reading is sent to Core 0. Whereat
		// Core 0 should save the data in order to compensate a given 
		// error in the next feeding process. (E.g. if the pump has
		// dispensed 2g too much, Core 0 should subtract 2g from the next
		// feeding command.)
		// ===============================================================

		switch (feedMode) {
			// +++++++++++++++++++++++++++++++++++++++++++++++++++++++++++++++++++++++++++++++++

		case PRIME:
			// Turn on secondary power
			Power_c1(true);													// (Support Function)

			// Prime Dumper Drive
			if (dumperReturn == BUSY) {
				dumperReturn = DumperDrive.Prime();
				if (dumperReturn == ERROR || dumperReturn == WARNING) {
					ReceiveWarningsErrors_c1(DumperDrive, MOTOR_0);			// (Support Function)
				}
			}

			// Wait for Dumper Drive to finish, then Prime Pump 1
			else if (pump1Return == BUSY) {
				pump1Return = Pump_1.Prime();
				if (pump1Return == ERROR || pump1Return == WARNING) {
					ReceiveWarningsErrors_c1(Pump_1, MOTOR_1);				// (Support Function)
				}
			}

			// Check if priming is finished.
			if (dumperReturn != BUSY && pump1Return != BUSY) {

				// Reset Flags
				dumperReturn = BUSY;
				feedMode = APPROX;

				// Correct feeding amount by past offset (when too much or too little food was dispensed last time)
				// Note, correction will be neglected if that leads to a feeding <= 1g or > MAX_SINGLE (see config).
				float newFA = feedingAmount_1 + feedingCorrection_1;
				if (newFA > 1 && newFA <= MAX_SINGLE) {
					feedingAmount_1 = newFA;
				}

				// Pump 1 - check amount to decide if approx. feeding is needed
				if (feedingAmount_1 <= APP_OFFSET) {
					// Approx. amount allready  reached, skip app. feeding.
					pump1Return = OK;
				}
				else {
					pump1Return = BUSY;
				}
			}
			break;
			// +++++++++++++++++++++++++++++++++++++++++++++++++++++++++++++++++++++++++++++++++

		case APPROX:
			// Do one cycle, then check if the desired amount (APP_OFFSET)
			// is reached (measure 2 times). If, then stop; if not, do another cycle.	

			// Pump 1
			if (pump1Return == BUSY) {
				if (Pump_1.MoveCycle() != BUSY) {
					if (Pump_1.Measure(2) >= feedingAmount_1 - APP_OFFSET) {
						// Approx. amount reached, ready for accurate feeding.
						pump1Return = OK;
					}
					else {
						// Increase feed cycles (checking for empty scale)
						feedCycles++;
					}
				}
			}

			// Check if approx. amount is reached
			if (pump1Return == OK) {
				// Reset feed cycles, flags and go to accurate feeding.
				feedCycles = 0;

				// Check if feeding amount is allready reached, then skip accurate feeding.
				// (Also, if feeding amount is set to 0.)
				if (Pump_1.Measure(5) >= feedingAmount_1 || feedingAmount_1 == 0) {
					pump1Return = OK;
				}
				else {
					// Amount not yet reached, Pump still busy / ready for accurate feeding.
					pump1Return = BUSY;
				}

				// Go to accurate feeding (will skip the actual steps if feeding amount is reached)
				feedMode = ACCURATE;
			}

			// Check if approx. amount is not reached after 10 cycles (at least one pump)
			if (feedCycles >= 10) {
				feedCycles = 0; // Reset feed cycles
				// Switch to emergency feeding, since approx.
				// amount is not reached after 10 cycles.
				PackPushData('E', 99, 6); // 99 - no device, 6 - Empty or scale broken (Support Function)
				Mode_c1 = EMGY;
			}
			break;
			// +++++++++++++++++++++++++++++++++++++++++++++++++++++++++++++++++++++++++++++++++

		case ACCURATE:
			// Accurate
			// Move slider in a precise filling motion until the desired amount is reached.

			// Pump 1
			if (pump1Return == BUSY) {
				if (Pump_1.MoveCycleAccurate() != BUSY) {
					if (Pump_1.Measure(3) >= feedingAmount_1) {
						// Final amount reached, ready for final step (EMPTY).
						pump1Return = OK;
					}
					else {
						// Increase feed cycles (checking for empty scale)
						feedCycles++;
					}
				}
			}

			// Check if accu. amount is reached
			if (pump1Return == OK) {
				// Reset feed cycles, flags and go to accurate feeding.
				feedCycles = 0;
				pump1Return = BUSY;
				feedMode = EMPTY;
			}

			// Check if accu. amount is not reached after 100 cycles (at least one pump)
			if (feedCycles >= 100) {
				feedCycles = 0; // Reset feed cycles
				// Switch to emergency feeding.
				PackPushData('E', 99, 6); // 99 - no device, 6 - Empty or scale broken (Support Function)
				Mode_c1 = EMGY;
			}

			break;
			// +++++++++++++++++++++++++++++++++++++++++++++++++++++++++++++++++++++++++++++++++

		case EMPTY:
			// Return slider back to home position, do final measurement, then empty the scales.

			// Pump 1
			if (pump1Return == BUSY) {
				// Move to home position
				if (Pump_1.MoveTo(0)) {

					// Do Final Measurement and send data to Core 0
					lastFed_1 = Pump_1.Measure(7);
					// (Uses floatToUint16 to convert measured float to uint16_t)
					PackPushData('A', SCALE_1, floatToUint16(lastFed_1));		// (Support Function)

					// Set correction for next feeding
					feedingCorrection_1 = feedingAmount_1 - lastFed_1;

					// Pump 1 is ready for emptying.
					pump1Return = OK;
				}
			}

			// Empty Scale if pumps is ready
			if (pump1Return == OK) {
				if (DumperDrive.EmptyScale() != BUSY) {

					// Reset flags, check for errors and go to IDLE.
					pump1Return = BUSY;

					// Update Food Level
					checkFillLevel_c1(floatToUint16(lastFed_1 / 100)); // (Support Function)

					// Check for warnings and errors
					ReceiveWarningsErrors_c1(DumperDrive, MOTOR_0);				// (Support Function)
					ReceiveWarningsErrors_c1(Pump_1, MOTOR_1);					// (Support Function)

					Mode_c1 = IDLE; // Back to IDLE
				}
			}
			break;
			// ++++++++++++++++++++++++++++++++++++++++++++++++++++++++++++++++++++++++++++++++*
		}
		break;
		// ----------------------------------------------------------------------------------------------------
	case CALIBRATE:

		// ===============================================================
		// Calibrates selected scales.
		// You can choose between verbose and silent calibration:
		// Verbose calibration: Shows calibration steps on Serial Monitor
		// Silent calibration will use the debug messeages / transmits
		// them to Core 0.
		// ===============================================================

		// Verbose calibration
		//Scale_0.CalibrateScale(true);

		// Silent calibration
		// -------------------------
		// CalStatus:
		// 0 - WAITING
		// 1 - TARE
		// 2 - PLACE_WEIGHT
		// 3 - CALIBRATING
		// 4 - SAVEING_CALIBRATION
		// 5 - FINISHED
		// 6 - CALIBRATION_ERROR
		// -------------------------
		// Calibrate Scale 1
		while (calStatus < 5) { // 5 = Calibration successful			
			// Calibrate
			calStatus = Pump_1.CalibrateScale(false);
			// Send calibration updates to Core 0.
			if (prevCalStatus != calStatus) {
				PackPushData('C', 1, calStatus);								// (Support Function)
				prevCalStatus = calStatus;
			}
			// (No need to implement error handling here, as it should be user detecable.)
		}

		// Reset CalStatus
		calStatus = 0;

		// Back to IDLE
		Mode_c1 = IDLE;

		break;
		// ----------------------------------------------------------------------------------------------------
	case AUTOTUNE:

		// ===============================================================
		// Autotunes stall detection for selected devices.
		// You can toggle "quick check" and "save to file":
		// Quick check: Will quickly check the stall detection, though
		// might not show the most accurate results (usually good enough).
		// Quick check set to false: Will be much slower but may give
		// more accurate results.
		// Save to file: Will save the stall values to NVM. Thus, they can
		// be loaded automatically on startup.
		// NOTE, stall values will be read from NVM if STALL_VALUE /
		// HOME_STALL_VALUE is set to 0. E.g. if only STALL_VALUE is set
		// to 0, only this will be read from NVM, but not for homeing.
		// NOTE, this is blocking code! If there is an error (stuck in
		// loop etc.), then only a restart will help.
		// WARNING, Autotune should start with the dumper driver.
		// Otherwise, food may block the pumps and cause damage!
		// ===============================================================

		// Turn on power
		Power_c1(true);												// (Support Function)	

		// Autotune Stall
		// (true/true for quick check and save to file)

		// Dumper Drive (Scales)
		while (DumperDrive.HomeMotor() == BUSY);
		DumperDrive.AutotuneStall(true, true);
		ReceiveWarningsErrors_c1(DumperDrive, MOTOR_0);				// (Support Function)

		// Pump 1
		while (Pump_1.HomeMotor() == BUSY);
		Pump_1.AutotuneStall(true, true);
		ReceiveWarningsErrors_c1(Pump_1, MOTOR_1);					// (Support Function)

		// Turn off power
		Power_c1(false);											// (Support Function)


		// Reboot PurrPleaser
		rp2040.reboot();

		/*
		// Back to IDLE
		Mode_c1 = IDLE;
		*/

		break;
		// ----------------------------------------------------------------------------------------------------
	case EMGY:
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

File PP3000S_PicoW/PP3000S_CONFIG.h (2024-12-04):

/*
* This is the configuration file for the PurrPleaser3000S (incl. 1x FoodPumps (+Scales) and 1x DumperDrive).
* The configuration file is optimized for the PurrPleaser3000S Board, however settings may be changed to fit other layouts.
* For different configurations, please change the settings below at "Configuration".
*/

#ifndef _PP3000S_CONFIG_h
#define _PP3000S_CONFIG_h

// Debugging
// --------------------------------------------------------------------------------
#define DEBUG_LEVEL DBG_NONE

/* Set desired debug level:
========================================================================
DBG_NONE - no debug output is shown
DBG_ERROR - critical errors
DBG_WARNING - non - critical errors
DBG_INFO - information
DBG_DEBUG - more information
DBG_VERBOSE - most information
Further info at: https://github.com/arduino-libraries/Arduino_DebugUtils
======================================================================== */
// -------------------------------------------------------------------------------*

// Configuration
// ----------------------------------------------------------------------------------------------------------------------------------------------------------------------------------------------------------------------------

    // NOTE: Credentials (your "secrets") are stored in the "credentials.h" file.
    // Please update your Wifi, MQTT and NTP credentials there!

    // This Purr Pleaser identifier
    //#define PP_ID     "PP_3000S"      // Purr Pleaser ID (Note, a unique HA ID is automatically generated with the device MAC Address.)
    #define PP_NAME     "Single Feeder" // Purr Pleaser Name (as shown at home assistant)
    #define VERSION     "0.1.0"         // Version of the Purr Pleaser
    #define PP_MODEL    "PP3000S"       // Model (e.g. PP3000S for Single Feeder, PP3000D for Double Feeder)

    // Cat Name
    #define NAME_CAT_1  "Maya"          // Name of the cat

    // Default Food Settings
    #define MAX_DAILY   80              // Max daily food amount (g) - as settable by Home Assistant
    #define MAX_SINGLE  20              // Max single food amount (g) - as settable by Home Assistant
    #define MIN_DAILY   0               // Min daily food amount (g) - as settable by Home Assistant
    #define MIN_SINGLE  0               // Min single food amount (g) - as settable by Home Assistant
    #define TREAT_AMT   1.0             // Default treat amount (g) - as settable by Home Assistant

    // Time Zone Settings (fill in your time zone settings)
    // (For info at: https://github.com/JChristensen/Timezone)
    // ============================================================================================================
    // Daylight Time (aka Summer Time)
    #define ABV_S       CEST    // Abrevation for Summer Time (name it as you like - no standard here)
    #define WEEK_S      Last    // Week of the month (First, Second, Third, Fourth, Last)
    #define DOW_S       Sun     // Day of the week (Sun, Mon, Tue, Wed, Thu, Fri, Sat)
    #define MON_S       Mar     // Month of the year (Jan, Feb, Mar, Apr, May, Jun, Jul, Aug, Sep, Oct, Nov, Dec)
    #define HOUR_S      1       // Hour at which the time changes
    #define UTC_S       60      // UTC offset in minutes (e.g. 0 for UTC +1)

    // Standard Time (aka Winter Time)
    #define ABV_W       CET     // Abrevation for Winter Time (name it as you like - no standard here)
    #define WEEK_W      Last    // Week of the month (First, Second, Third, Fourth, Last)
    #define DOW_W       Sun     // Day of the week (Sun, Mon, Tue, Wed, Thu, Fri, Sat)
    #define MON_W       Oct     // Month of the year (Jan, Feb, Mar, Apr, May, Jun, Jul, Aug, Sep, Oct, Nov, Dec)
    #define HOUR_W      2       // Hour at which the time changes
    #define UTC_W       0       // UTC offset in minutes
    // ============================================================================================================

    // PurrPleaser Board Settings
    #define EXPANDER            false       // Use expander (true) or not (false); if false settings below are ignored
    #define MCP_ADDRESS         0x20        // Port expander address
    #define MCP_INTA            1           // Interrupt pin A	- IMPORTANT: SET TO 1 FOR HOMING WITHOUT MCP23017!!!
    #define MCP_INTB            99          // Interrupt pin B
    #define SLC_PIN             99          // SLC pin
    #define SDA_PIN             99          // SDA pin
    #define VV_EN               99          // 5V Enable Pin (99 = not used)
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

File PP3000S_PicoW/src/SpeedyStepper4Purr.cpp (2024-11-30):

//      ******************************************************************
//      *                                                                *
//      *                      Speedy Stepper 4 Purr                     *
//      *								 *
//      *            Poing3000                       20/07/2023          *
//      *                   Copyright (c) Poing3000, 2023                *
//      *								 *
//      *			   Original from			 *
//      *                   Speedy Stepper Motor Driver                  *
//      *                                                                *
//      *            Stan Reifel                     12/8/2014           *
//      *               Copyright (c) S. Reifel & Co, 2014               *
//      *                                                                *
//      ******************************************************************


// MIT License
// 
// Updates Copyright (c) 2023 Poing3000
// Original Copyright (c) 2014 Stanley Reifel & Co.
// 
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

//
// This library is used to control stepper motors in the PurrPleaser3000 Cat Feeding Machine Projects.
// For further info on the usage of this libray please find the superior documentation at the original
// repository "SpeedyStepper4Purr" library from S. Reifel.
//
// Changes implemented:
// > Reduced to "steps/second" functions (deleted per Revolution and Distance functions).
// > Adapted Homing function to (almost) non - blocking code, advanced error detection/handling
//	 and the possibility to change end stop inputs (i.e., from an end stop to driver stall detection).
//	> NOTE, if the end stop pin (homeEndStopNumber) is set to 99, the end stop signal is expected from an external source / function (see move home).
//  > NOTE, error handling is BLOCKING code.
// > WARNING, limited to 4 steppers, as only 4 interrupt pins are available (see switch below).

// =====================================================================================================


#include "SpeedyStepper4Purr.h"

// ---------------------------------------------------------------------------------
//                                  Setup functions 
// ---------------------------------------------------------------------------------


// Constructor for the stepper class
SpeedyStepper4Purr::SpeedyStepper4Purr(const byte whichDiag) : whichDiag_ (whichDiag)
{
  // initialize constants
  stepPin = 0;
  directionPin = 0;
  homeEndStop = 0;
  homeDiagPin = 0;
  currentPosition_InSteps = 0;
  desiredSpeed_InStepsPerSecond = 200.0;
  acceleration_InStepsPerSecondPerSecond = 200.0;
  currentStepPeriod_InUS = 0.0;
  homingState = NOT_HOMING;
  flagStalled_ = false;

}

//  Connect the stepper object to the IO pins
//  Enter:  stepPinNumber = IO pin number for the Step
//          directionPinNumber = IO pin number for the direction bit
// 			homeEndStopNumber = IO pin number for the home limit switch
// 			homediagPinNumber = IO pin number for the driver stall detection.
//				>>NOTE: this limits the number of steppers to 4, as only 4
//						interrupt pins are available (see switch below).
//
void SpeedyStepper4Purr::connectToPins(byte stepPinNumber, byte directionPinNumber, byte homeEndStopNumber, byte homeDiagPinNumber)
{
  // Remember the pin numbers
  stepPin = stepPinNumber;
  directionPin = directionPinNumber;
  homeEndStop = homeEndStopNumber;
  homeDiagPin = homeDiagPinNumber;
  
  // Configure the IO bits
  pinMode(stepPin, OUTPUT);
  digitalWrite(stepPin, LOW);

  pinMode(directionPin, OUTPUT);
  digitalWrite(directionPin, LOW);

  // Configure the home end stop; if 99, the end stop signal is provided from an external source / function (see move home).
  if (homeEndStop != 99) {
	  pinMode(homeEndStop, INPUT_PULLUP);
  }


  //Assign interrupts for stall detection. Limited to 4 steppers, as only 4 interrupt pins are available (see switch below).
  switch (whichDiag_) {
	case 0:
		attachInterrupt(digitalPinToInterrupt(homeDiagPin), StallInterrupt0, RISING);
		instance0_ = this;
		break;
	case 1:
		attachInterrupt(digitalPinToInterrupt(homeDiagPin), StallInterrupt1, RISING);
		instance1_ = this;
		break;
	case 2:
		attachInterrupt(digitalPinToInterrupt(homeDiagPin), StallInterrupt2, RISING);
		instance2_ = this;
		break;
	case 3:
		attachInterrupt(digitalPinToInterrupt(homeDiagPin), StallInterrupt3, RISING);
		instance3_ = this;
		break;
  }
}

//Interrupt glue routines
void SpeedyStepper4Purr::StallInterrupt0() {
	instance0_->StallIndication();
}
void SpeedyStepper4Purr::StallInterrupt1() {
	instance1_->StallIndication();
}
void SpeedyStepper4Purr::StallInterrupt2() {
	instance2_->StallIndication();
}
void SpeedyStepper4Purr::StallInterrupt3() {
	instance3_->StallIndication();
}


//for use by interrupt glue routines
SpeedyStepper4Purr * SpeedyStepper4Purr::instance0_;
SpeedyStepper4Purr * SpeedyStepper4Purr::instance1_;
SpeedyStepper4Purr * SpeedyStepper4Purr::instance2_;
SpeedyStepper4Purr * SpeedyStepper4Purr::instance3_;

void SpeedyStepper4Purr::StallIndication() {
	flagStalled_ = true;
}


// ---------------------------------------------------------------------------------
//									Public functions
// ---------------------------------------------------------------------------------


// Set the current position of the motor, this does not move the motor
// Note: This function should only be called when the motor is stopped
//	Enter:  currentPositionInSteps = the new position of the motor in steps
//
void SpeedyStepper4Purr::setCurrentPositionInSteps(long currentPositionInSteps)
{
  currentPosition_InSteps = currentPositionInSteps;
}


// Get the current position of the motor, this functions is updated
// while the motor moves
//	Exit:  a signed motor position in steps returned
//
long SpeedyStepper4Purr::getCurrentPositionInSteps()
{
  return(currentPosition_InSteps);
}
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

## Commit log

2024-12-23 Update schematics
2025-01-24 Improve Food Level Readings
    - Fix the issue where food refilled below the top sensor is not recognized by the feeder when food was before below the low sensor. The support function checkFillLevel_c1 should be reworked in the future, as it is functional but could be improved and remains slightly buggy.
    - Food level sensors are now read every 10 seconds while idle, allowing for updates to food level readings, not just after feeding.
    [PP3000S_PicoW.ino, SupportFunctions.h]
2025-06-21 Add POWMAN timer compatibility
2025-06-21 docs: clarify powman timer requirements and update comments
